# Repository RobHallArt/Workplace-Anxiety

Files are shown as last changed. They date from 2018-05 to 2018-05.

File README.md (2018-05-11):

# Workplace-Anxiety
Code to control a fleet of arduino based machines based on presence of users detected by an XBOX Kinect V2 Sensor

# IDEATION
In this project I use physical computing devices such as Arduino boards, integrated circuits and servos, to build a fleet of machines that will inhabit traditional work spaces. Machines are taking over from human in jobs that it was thought were impossible to automate. This creep of digital automation, takes over jobs without physically manifesting itself in the workplace. The machines are a reminder that automation is still happening.

The machines are presented in a social state, as a fleet, appearing to converse. This changes how they are perceived; by displaying the machines in this way introduces them to a space in the workplace normally an escape for humans. The machines converse in their own language, impenetrable to humans, which excludes the human from a previously exclusive social environment. I imagined that the machines were taking over in a similar fashion to a hostile takeover of a company. The machines will cease conversations when they detect a human nearby, and turn to face the interloper with accusative, piercing, red eyes. This last part was always important to me as it creates a sudden unease in the audience. 

When conversing, the machines diminutive size and squeaky 'voices' could make them seem cute, especially on their own. I attempted to counter this by creating a design that was somewhat industrial, using metal bolts to hold the machines and their frames together to give an industrial feel. Bare materials play a part too, exposed circuitry and burned wood from laser cutting. Early on I printed head assemblies using coloured 3D printer filament, but added a black fascia attached with bolts, to mitigate this. The machines really become sinister when they are part of a fleet. One machine tracking you with it's eyes as you move around it is not particularly effective, but seven machines acting independently is overwhelming.

All along I had the scenario in my head of conversations stifled by the arrival of the subject of such conversation. The sense of exclusion was the foundation of the project as that is exactly how I see the takeover of machines manifesting itself.

# TECHNICAL
This project has taught me a huge amount about physical computing. I have tested, ruled out and selected various solutions and techniques for almost every part of the machines and their build process. I learned lessons ranging from how to build a serial communication protocol to the disadvantages of ordering parts from china.

I started my project by building a simple demo in processing that took an input from an XBOX Kinect sensor and used it to draw the space in front of the sensor as a top down plan of the space with people in the space marked as points derived from the X and Z values of the pelvic point from the Kinect skeleton. The sketch also featured a pointed shape that rotated to point always at the person the Kinect was tracking. This small piece of code became the foundation for most of this project, but it was only the beginning.

The next step then was to communicate the coordinates of the person in the room to each of the machines, as I always knew I wanted a fleet. My original idea was to have the machines communicate using sound, I quickly gave up on this however as I could foresee difficulty building a protocol that would prevent machines interfering with one another. I did however know that the machines needed to be wireless, in order to appear to be acting autonomously.

My research first brought me a set of generic 433 Mhz Transmitter and Receiver boards. While low cost, these boards were riddled with flaws from the outset, as the Arduino library that controls them conflicts with that which controls servos. This coupled with interference issues and general lack of support forced me to move on. My next option was WiFi communication using 'esp8266' boards, which in theory offered numerous benefits. My research told me the boards could be programmed using the default Arduino language and Integrated Development Environment (IDE), that they could be meshed together offering a very low latency and very reliable system. In reality however they were very difficult to program because they require a separate programmer and also do not conform to standard pin spacing conventions meaning every board would require ribbon cables to be soldered to them. I finally settled on the HC-12 board for communication as it is widely supported and allows communication over serial. The softwareSerial library essentially allowed me to write serial commands as I had when communicating from processing to Arduino over USB and have them sent to as many other Arduinos as I liked.

The next problem came in writing a protocol that was resistant to the odd interruption; I needed to build in error correction. This was completely new territory for me as it was the first time I had programmed wireless communication without the backbone of an library such as webSocket with built in error checking and correction. I ended up checking the message by making sure every update was fixed length. For example rather than sending just '25' for an X position of 25, I would send '025'. This worked because interference manifested itself in the communication far more often as dropped characters than incomplete or corrupted characters. Any time three digits for any value were not received the whole message was discarded.

Another challenge I faced was that not all of the pins on the Arduino are the same, and despite some being marked as allowing Pulse Width Modulation (PWM), there seemed to be no connection between this and which pins worked for what task. After much trial and error I had a plan for a pin layout that allowed all the devices connected to each Arduino to function properly. I ended up with 2 pins for the HC-12, one pin for the Servo and three PWM pins for the Red, Green and Blue pins of the LEDs for the eyes.

My choice of LEDs was a design choice I didn't take lightly. I knew I wanted LEDs as large and bright as possible, but I couldn't decide between cloudy and clear plastic for the top of them. They had vastly different effects. The cloudy LEDs produced diffuse light and almost appeared to just glow with the selected. I devised a test whereby I programmed an Arduino to strobe an array of LEDs, which I would then stare directly into, simulating eye contact with the machine. I very quickly determined that I could easily look at the cloudy LEDs without any effects, the clear LEDs however were piercing, with the curved plastic focusing the light into a point at the front of the LED. My choice was clear.

For power I used 18650 type rechargeable Li-Po Batteries connected to the Vin pin of the Arduino through a step up voltage regulator that adapts the P.D from 3.7v to 5v. This proved to be a surprisingly inexpensive solution as power had been one area where I had expected to spend more money on the project.

# CONSTRUCTION
Once I had completed a circuit diagram in fritzing, I began to solder together boards with female pins for the Arduino and HC-12 and male pins for the servo and LED wires as I wanted to be able to salvage the expensive parts at a later date. My first few attempts were a mess, and while functional did not use space on the board efficiently. As my soldering improved, so did my planning of where to route wires and solder connections so as to use as little wire as possible with minimal overlap. Over the iterations this caused the design of the board to become standardised.

The head elements were 3D printed to fit the LED boards I had created. Measurements were taken of the servo mount and the LED board using calipers and the design was created in Fusion 3D. Three mounts were printed before one was a good fit for both the LED assembly and the servo.

Next came the Base. I had thought of 3D printing this too but it turned out to be much easier to use the laser cutter. I made a prototype in cardboard before beginning to print the real thing in wood. It took 5 prints of 10 minutes for all the parts to be finished.

The design for both the head assembly and the base was utilitarian. I decided this was achievable given my level of proficiency with Fusion 3D, it also reflects the stark, functional nature of the code the machines represent. A later choice was also made to add a fascia to the front of the head assembly, this played two purposes, it was printed in black so as to mask the coloured material of the actual head assembly, and also provided screw holes through which the LED assembly is attached permanently.

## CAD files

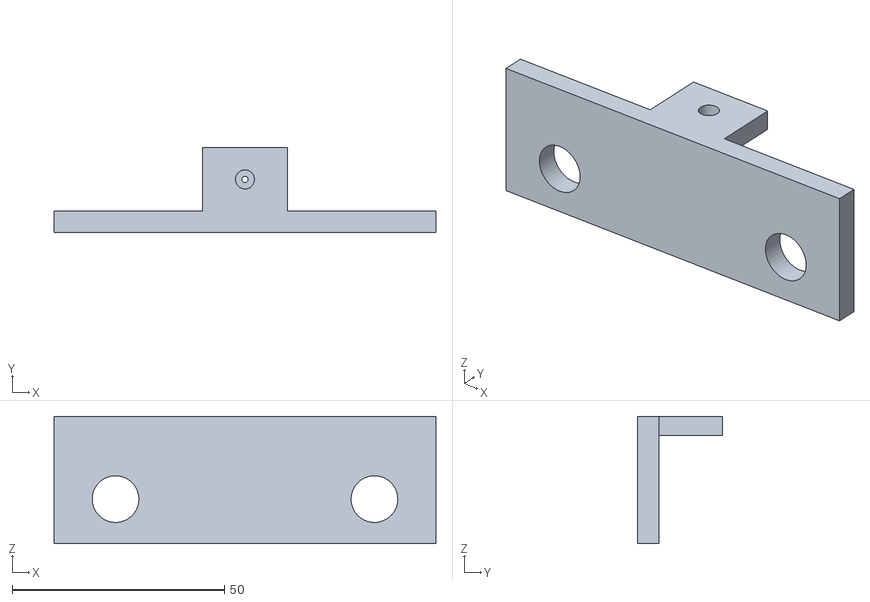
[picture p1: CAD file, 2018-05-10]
Physical Manufacture Files/Head Assembly for 3D Print.stl
90.0 x 20.0 x 30.0

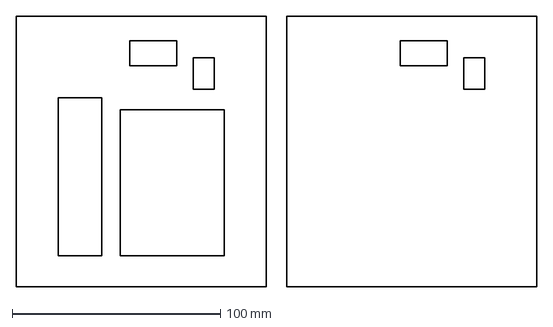
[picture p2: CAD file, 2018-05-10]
Physical Manufacture Files/Platform Square.dxf
250.0 x 130.0 mm

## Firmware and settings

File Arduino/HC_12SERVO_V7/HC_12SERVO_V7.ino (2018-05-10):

#include <Servo.h>              // import servo library
#include <SoftwareSerial.h>     // import serial library for HC-12

String readString;

int machineID = 1;              // unique ID of each machine

int machineX = 30;              // unique position of machine in 180x180 grid
int machineY = -20;

int timeLastMessage = 0;        // set to the millis(); value every time a message is recieved to keep track of time since last message

int recievedX = 0;              // position of user received from serial
int recievedY = 0;

int toneLevel = 3000;           // base value for frequency used for 'speech'

int r2count = 0;                // counter to keep track of the iterations of the r2D2seq speech function
int servoVal = 1;               // value read from servo to keep head motions less than 50 degrees for any one movement
int calcVal = 0;                // value calculated from recievedX and recievedY using atan2()


int speakerPin = 2;             // set pins for all devices attached to arduino.
int rPin = 3;
int gPin = 5;
int bPin = 6;
int servoPin = 8;
int HC12TX = 9;
int HC12RX = 10;

const int numReadings = 10;     // how many recieved numbers are averaged

int readings[numReadings];      // recieved data
int readIndex = 0;              // index of the current data
int total = 0;                  // running total
int average = 0;                // average

SoftwareSerial HC12(HC12TX,HC12RX);   // create instance of SoftwareSerial for the HC-12 chip
Servo myservod;                       // create instance of Servo for our single servo.

void setup() {

        HC12.begin(115200);                 // start serial communication with the HC-12 board at a baud rate (data rate) of 115200 bits per second
        Serial.begin(115200);               // start serial communication any connected PC at a baud rate (data rate) of 115200 bits per second
        Serial.println("RECIEVER GO");      // send startup complete message to connected PC

        randomSeed(analogRead(0));          // read value from a disconnected pin to seed randomness and prevent machines using the same random values

        // initialize all the readings to 0:
        for (int thisReading = 0; thisReading < numReadings; thisReading++) {
                readings[thisReading] = 0;
        }

        pinMode(speakerPin, OUTPUT);        // set pinModes for all non-data pins
        pinMode(rPin,OUTPUT);
        pinMode(gPin,OUTPUT);
        pinMode(bPin,OUTPUT);

        myservod.attach(servoPin);          // connect instance of Servo to correct pin for servo

        setColour(0,255,0);                 // set LEDs to green to indicate successful startup
        myservod.write(90);                 // move servo to central position to calibrate
        delay(1000);                        // wait one second
        setColour(0,0,0);                   // turn LEDs Off
        delay(1000);                        // wait one second before beginning main program
}

void loop() {
        if (HC12.available()) {                                 // when HC-12 is recieving
                setColour(255,0,0);                             // set LEDs to red
                timeLastMessage = millis();                     // set current tome to timeLastMessage
                char c = HC12.read();                           // gets one byte from serial buffer

                if (c == ',') {                                 // if most recently revieved byte is ','
                        if (readString.length() == 3) {         // check if message is 3 bytes long for error detection

                                int n = readString.toInt();     // convert message into a number
                                Serial.print("Y");              // send value to connected PC (for Debugging)
                                Serial.println(readString);
                                recievedY = n;                  // set value of n to recievedY as it will be reset later

                        }

                        readString="";                          // clears variable for new input

                } else if (c == '-') {                          // if most recently revieved byte is '-'
                        if (readString.length() == 3) {         // check if message is 3 bytes long for error detection

                                int n = readString.toInt();     // convert readString into a number
                                Serial.print("X");              // send value to connected PC (for Debugging)
                                Serial.println(readString);
                                recievedX = n;                  // set value of n to recievedX as it will be reset later

                        }

                        readString="";                          // clears variable for new input

                } else if (c == '.') {                          // if most recent byte is '.' this indicates message conclusion and triggers the calculation and servo code

                        setColour(255,0,0);                     // set LEDs to red

                        calcVal = abs(180-atan2(recievedY - machineY, recievedX - machineX) * 57296 / 1000);
                        // arc tangent is used to calculate the direction the servo is pointing
                        // it is multiplied by 57296 / 1000 to convert from radians to degrees
                        // the arduino is slow at calculating with decimals so we try to keep everything in integers


                        total = total - readings[readIndex];    // remove the oldest servo position from the total
                        readings[readIndex] = calcVal;          // add the most recent calculated servo position to the array
                        total = total + readings[readIndex];    // add the most revent calculated servo position to the total
                        readIndex = readIndex + 1;              // advance to the next position in the array

                        if (readIndex >= numReadings) {         // if end of array is reached
                                readIndex = 0;                  // return to start of array
                        }

                        average = total / numReadings;          // calculate average
                        myservod.write(average);                // send average value to servo
                        Serial.print("ANGLE");                  // send angle to connected PC (for Debugging)
                        Serial.print(average);
                        Serial.println();

                } else {                              // if the most recent byte isn't a control character, continue reading
                        readString += c;              // adds most revent byte to the string of recieved bytes
                }
        }

        if(abs(timeLastMessage-millis())>1000) {      // if it has been more than a second since the last message run the 'speech' function
                r2D2seq();                            // run the speech function
        }
}

void beep (int speakerPin, float noteFrequency, long noteDuration){

        //Beep function from https://github.com/IoTMakers/Arduino

        int x;
        // Convert the frequency to microseconds
        float microsecondsPerWave = 1000000/noteFrequency;
        // Calculate how many HIGH/LOW cycles there are per millisecond
        float millisecondsPerCycle = 1000/(microsecondsPerWave * 2);
        // Multiply noteDuration * number or cycles per millisecond
        float loopTime = noteDuration * millisecondsPerCycle;
        // Play the note for the calculated loopTime.

        for (x=0; x<loopTime; x++) {

                digitalWrite(speakerPin,HIGH);
                delayMicroseconds(microsecondsPerWave);
                digitalWrite(speakerPin,LOW);
                delayMicroseconds(microsecondsPerWave);

        }
}

void r2D2seq(){                                      // 'speech' synthesis function

        // this function uses randomness inserted at different levels at varying frequency to create speech in as natural a way as possible
        // the pitch of the 'voice' changes every 20 'words', with the chance of a pause every time the function is run
        // longer pauses are less likely and therefore less frequent

        if(r2count%20 == 0) {                        // if the counter of times the function has been run is divisible by 20, set a new pitch for the voice

                toneLevel = random(0,500);           // set the base pitch to a value between 0 and 500 (Hz)

        }

        if(random(0,100)<60) {                       // pick a random value from 0 to 100 and check if it is less than 60

                setColour(random(0,255),random(0,255),random(0,255));                   // set LEDs to a random colour.
                servoVal = myservod.read()+random(-50,+50);                             // read from servo and find a value within 50 degrees of that position
                myservod.write(constrain(servoVal,5,175));                              // constrain value to the servo boundaries and write it to the servo
                beep(speakerPin,random(toneLevel+20,toneLevel+300),random(20,200));     // use base pitch to calculate a more granular pitch and play for a random period up to 0.2 seconds

        } else if(random(0,100)<10) {                // pick a random value and check if it is less than 10

                setColour(20,50,20);                 // set LEDs to a darker greenish hue
                delay(4000);                         // wait 4 seconds to simulate listening to another machine

        } else {                                     // if none of the above is true

                setColour(20,50,20);                 // set LEDs to a dark greenish hue
                delay(random(20,400));               // wait for a shorter period between 0.02 and 0.4 of a second

        }

        r2count = r2count + 1;                       // increment fucntion counter
}

void setColour(int _red, int _green, int _blue){     // simple function to streamline setting LED colour

        analogWrite(rPin,_red);                      // set each pin based on passed values
        analogWrite(gPin,_green);
        analogWrite(bPin,_blue);

}

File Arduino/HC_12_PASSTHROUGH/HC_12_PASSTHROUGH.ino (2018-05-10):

#include <SoftwareSerial.h>                      // import SoftwareSerial library for HC-12

SoftwareSerial HC12(4,5); // RX,TX               // initialise SoftwareSerial instance with HC-12 pins

void setup() {

        Serial.begin(115200);                    // begin communication with PC at 115200 bits per second
        HC12.begin(115200);                      // begin communication with HC-12 115200 bits per second these must match to prevent sync issues
}

void loop() {

        while(HC12.available()) {                // while HC-12 is recieving
                Serial.write(HC12.read());       // send to PC via standard Serial
        }

        while(Serial.available()) {              // while recieving from connected PC
                HC12.write(Serial.read());       // send to HC-12 to send to machines
        }
}

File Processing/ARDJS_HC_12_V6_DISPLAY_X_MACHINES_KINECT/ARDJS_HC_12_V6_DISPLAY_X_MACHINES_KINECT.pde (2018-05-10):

import processing.serial.*;                           // import libraries
import KinectPV2.KJoint;
import KinectPV2.*;

Serial myPort;                                        // create instance of Serial with which we will talk to the HC-12 Passthrough board.
KinectPV2 kinect;                                     // create instance of KinectPV2 to handle the Kinect tracking

int areaX = 180;                                      // define the area of the trackable field
int areaY = 180;

PVector[] machines = new PVector[7];                  // create 7 machines as an array of PVectors

public int kinectyPos;                                // create public variables for the tracking data we get from the kinect
public int kinectxPos;


void setup(){
        size(1024,600);                               // set size to 1024x600 as this is the resolution of the handheld screen used to operate this sketch
        //fullScreen();                               // sketch is set to fullScreen when running on handheld display
        frameRate(20);                                // limit framerate to 20 to limit the frequency of draw() calls in tern limiting frequency of Serial calls to prevent overloading of the Arduino

        ellipseMode(CENTER);                          // draw ellipses from the center to reduce confusion down the line

        kinect = new KinectPV2(this);                 // initialise instance of KinectPV2
        kinect.enableColorImg(true);                  // enable the full spectrum camera in the Kinect
        kinect.enableSkeleton3DMap(true);             // enable Kinect skeleton tracking
        kinect.init();                                // initialise the Kinect with these parameters

        String portName = Serial.list()[0];           // open a serial port to the Arduino using the first open COM channel (only one connected)

        machines[0] = new PVector(0,0);               // set positions of each machine in the trackable field
        machines[1] = new PVector(30,-20);
        machines[2] = new PVector(60,-30);
        machines[3] = new PVector(90,-40);
        machines[4] = new PVector(120,-30);
        machines[5] = new PVector(150,-20);
        machines[6] = new PVector(180,0);

        for(int i = 0; i<Serial.list().length; i++) {           // loop through available COM ports
                println(Serial.list()[i]);                      // print each to the console (for debugging)
        }
        myPort = new Serial(this, portName, 115200);            // initialise the Serial port with a baud(data) rate of 115200 bits per second
}

void draw(){

        background(0);                                          // set background to black to clear screen each frame
        image(kinect.getColorImage(), 0, 0, 640, 368);          // display color image from kinec tot the left of the screen

        ArrayList<KSkeleton> skeletonArray =  kinect.getSkeleton3d();       // get the array of skeletons for this frame

        for (int i = 0; i < skeletonArray.size(); i++) {                                          // iterate through every skeleton in the skeleton array
                KSkeleton skeleton = (KSkeleton) skeletonArray.get(skeletonArray.size()-1);       // get the skeleton of the most recent person to enter the visual field

                if (skeleton.isTracked()) {                                                       // while the skeleton is tracked
                        KJoint[] joints = skeleton.getJoints();                                   // get array of joints from the skeleton
                        kinectxPos = constrain(int(map(joints[KinectPV2.JointType_SpineBase].getX(),-1.55,1.55,0,180)),0,180)-20;             // calculate a position for the base of the user's spine in the 2D trackable field
                        kinectyPos = constrain(int(map(joints[KinectPV2.JointType_SpineBase].getZ(),1.85,3,0,180)),0,180);

                        if(map(kinectyPos,0,areaX,0,180)<180) {              // if the y position of the user is less than 180, then they are being tracked

                                // the write command here sends two values to the Arduino in a manner that allows for error correction later
                                // the command sends the position in the form "xxx-yyy,." this means that even if the number is 1 (001) or 125 (125) three digits are always sent
                                // the Arduino checks for three digits when it recieves the values, if there are not 3 values the message is discarded
                                myPort.write(nf(int(map(kinectxPos,0,180,0,180)),3)+"-"+nf(int(map(kinectyPos,0,180,0,180)),3)+"," +".");
                                println(nf(int(map(kinectxPos,0,180,0,180)),3)+"-"+nf(int(map(kinectyPos,0,180,0,180)),3)+"," +".");          // the sent data is also printed to the console for debugging
                                pushMatrix();                                       // push the matrix so that we can draw a visual representation of the tracked space to the right of the live image
                                translate(700,50);                                  // the start point for drawing is moved 700 pixels right and 50 down, so it is beside the getColorImage
                                fill(255,0,0);                                      // set the fill colour of drawn elements to red
                                ellipse(kinectxPos,kinectyPos,5,5);                 // draw the position of the trakced user in the space
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
